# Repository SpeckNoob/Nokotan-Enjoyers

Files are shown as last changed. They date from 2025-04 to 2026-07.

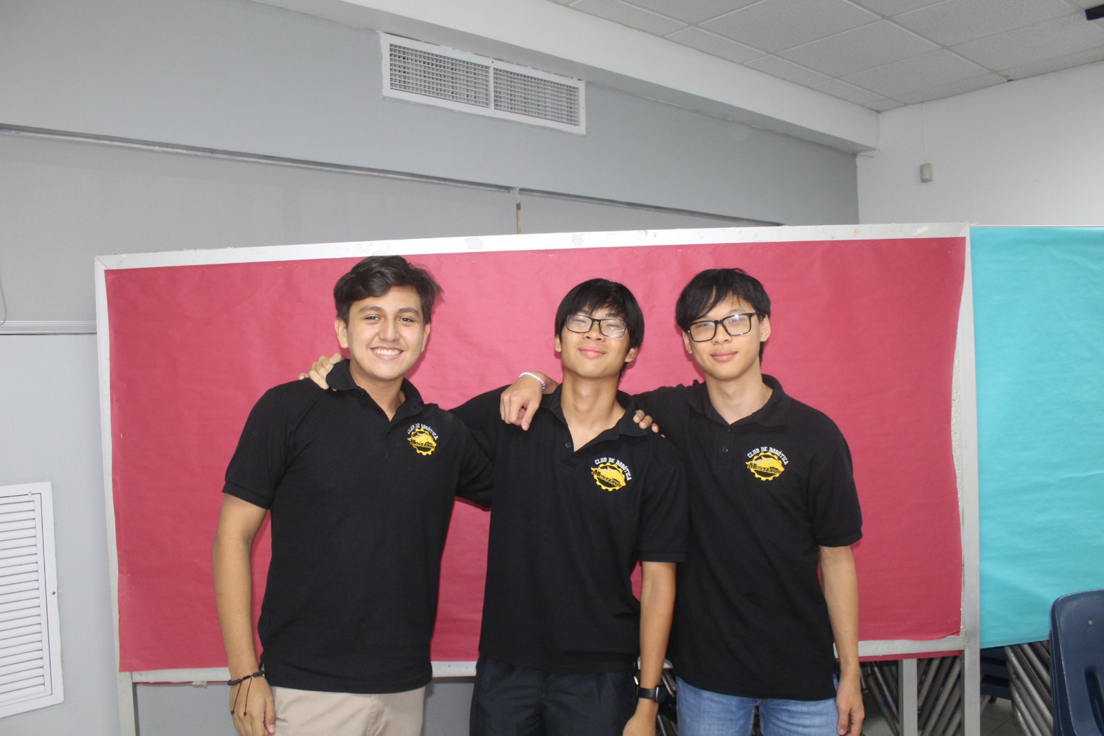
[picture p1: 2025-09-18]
t-photos/pictures/342e0a49-aa14-48cb-8f80-8e314d3dc333.jpeg

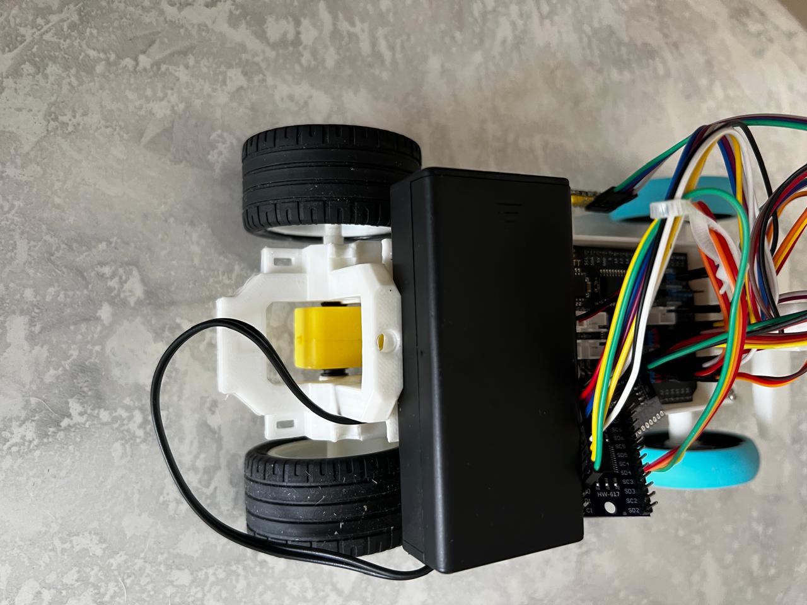
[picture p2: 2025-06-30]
v-photos/wro robot back.jpg

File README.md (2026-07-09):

Mustangs Down
====

<p align="center">
  Demo animation
</p>

This repository contains the documentation for the Mustangs Down team's robot for the 2025 World Robot Olympiad Future Engineers category competition. The robot was designed and built by a team of three.

Table of contents
----

- [The Team](#the-team)
- [The Competition](#the-competition)
- [Photos of the robot](#photos-of-the-robot)
  - [Video](#video)
- [Motors, sensors and systems](#motors-sensors-and-systems)
  - [Movement](#movement)
- [Steering](#steering)
  - [Servo Motor](#servo-motor)
- [Motherboard](#motherboard)
- [Skeleton/Chassis](#skeleton/chassis)
- [Energy Management](#energy-management)
  - [Battery](#battery)
- [Sensors](#sensors)
  - [Multiplexer](#multiplexer)
- [Circuit Diagram](#circuit-diagram)
- [Program and Source Code](#program-and-source-code)
  - [Drive](#drive)
  - [Open Round](#open-round)
  - [Obstacle Round](#obstacle-round)
  - [Camera](#camera)

## The Team
----

Mark Chen, Age: 16



School: Panamerican School of Panama, PAS

Hi!, I'm Mark from Panama with Chinese origin born in February 8 2009. I've been participating in WRO since 2022 and this is my second year participating in the Future Engineers category. I enjoy playing piano and I am a part of a school band, other hobbies include cubing (Rubik's cube competitions), gaming, drawing and volleyball.

----

Juan Pablo Gomez, Age: 16



School: Panamerican School of Panama, PAS

Hi, I'm Juan Pablo, from Colombia. I love robotics. I've been working with robots since I was 8 years old. My main hobbies are playing bass, hanging out with friends, playing video games, driving karts, and participating in various sports such as football and volleyball.

----

Julio Chong, Age: 16



School: Panamerican School of Panama, PAS

My name is Julio Chong, a panamenian teen with chinese antescedents who was born in August 24, 2008. I've been into robotics since 9th grade on 2023. My hobbies are playing the guitar, cooking, coding, learning new languages and also doing lots of exercise or sport, especially contact sports such as jiujitsu.

----

Victor Sanchez (Coach), Age: 35



School: Panamerican School of Panama, PAS

Hello, I'm Victor Sanchez, robotics profesor with experience in educational programming with LEGO SPIKE in Panamerican School, I've led the robotics scholar proyect for 4 years with the goal of becoming national champion in Panama and solid at an international scale. I enjoy woodworking and playing videogames.

----

Team photo
----



[Back to table of contents](#table-of-contents)

The competition
----

Unlike the structured missions of other WRO categories, Future Engineers presents a broad problem (often related to autonomous vehicles, smart systems, or complex automation), and teams must engineer a full solution. Teams work within defined technical limits (size, cost, sensors, etc.) that mimic real-life engineering conditions. This challenge has two main tasks, the first round which tests the robot's progamming of being able to drive many laps without crashing. The second round adds obstacles that the robot must avoid crashing into and a parking space where the robot should finish.

This challenge emphasizes all aspects of the engineering process, including:

- Mobility: Developing efficient vehicle movement.

- Obstacle managing: Detecting and dodging the different obstacles (Green and Red blocks) with effiency.

- Documentation: Showcasing engineering progress, design planning, and collaboration though a GitHub repository.

Points are awarded based on the performance of the robot. In the first round, points are awarded if the robot does not crash or stop during the round. In the second round, points are awarded for every obstacle the robot is able to detect and avoid, bonus points are rewarded if the robot can succesfully finish in the designated parking space.

[Back to table of contents](#table-of-contents)

## Photos of the robot
----

| Top | Bottom |
|---|---|
| WhatsApp Image 2025-09-29 at 17 31 00_9bd73e38 |WhatsApp Image 2025-09-29 at 17 31 00_5592dadc |

| Left | Right |
|---|---|
| WhatsApp Image 2025-09-29 at 17 31 00_614abe10 |WhatsApp Image 2025-09-29 at 17 31 00_24b984a5 |

| Front | Back |
|---|---|
|WhatsApp Image 2025-09-29 at 17 31 01_d4408ce1 |WhatsApp Image 2025-09-29 at 17 31 01_3e9ea6a2 |

## Video
---

Video of the robot on Youtube: [Video](https://youtu.be/vqMiVIuP070)

[Back to table of contents](#table-of-contents)

## Motors, sensors and systems
----

The robot operates with multiple motors and sensors which will be showcased here.

## Movement
----
The robot uses motors for drving and steering, these components work together to ensure the robot has a smooth and efficient movement.



|  Voltage | Current  | rpm |  Torque  |
|---|---|---|---|
| 3 | 160 | 120 | 0.45 |
| 6 | 220 | 200 | 1.0 |
| 7.2 | 250 | 250 | 1.5 |

We chose this motor because it was viable and the one we had already, other motors we used didn't hold up or didn't have enough power to move the wheels. Although there are way better motors we could've bought, we chose this one for its dual motor and it didn't need a driving axle. This made the building process a bit easier and less complicated.

The motor works by converting electrical energy into mechanical energy, specifically rotational motion, through the interaction of magnetic fields. It uses the principle that a current-carrying conductor experiences a force within a magnetic field. This force causes a rotor to spin, which then drives a shaft, producing mechanical work. This is then connected to the wheels with two jammed axles.

To connect the motor to the skeleton, we made an opening in the skeleton to fit the motor inside, then we held it up with a bent metal sheet and some screws.



The design could be perfected if the skeleton was made to scale with the motor or we had chosen a different motor that not only satisfies what the robot needs but also that it fits confortably to the skeleton.



(Full model is in the "models" repository)

## Steering
----
We experimented with many steering mechanisms but the one we found most success was anti-Ackerman steering. Other methods where either too big and complex or didn't turn the right amount. Anti-Ackerman systems are usually used on racing cars where the vehicles must turn at high speeds and the tires might slip, the outer tire’s increased steering angle helps compensate for these slip angles, maximizing grip during high-speed cornering. Even though with this robot we can't reach those speeds where the wheels start slipping, the anti-Ackerman system is still the most effective and simple for this competition.

The steering system is composed of two identicar wheel holders connected with two steering axels, these two axels are then connected to the servo motor in the middle.



## Servo motor:
----

 

|  Voltage | Temperature | Angle of Rotation | Torque |  Control signal  |  Type of Servo  |
|---|---|---|---|---|---|
|  3.3V~5V | -30°C~+60°C | 180 | 1.6KG/cm | PWM signal |  Digital servo  |

For the motor we used the Steren servo motor, it's an okay motor but we chose it because it was the one we had in hand. Although it is a cheap motor, it works perfectly with the design of the robot. It also operates on low voltage (4.8–6V) and provides moderate torque for small mechanisms.



The motor is placed between both axels to form an anti-ackerman system

## Motherboard
----



| Chip | Clock | ROM |  SRAM  |  FLASH  | Interfaces |  Input voltages  |
|---|---|---|---|---|---|---|
| ESP-WROOM-32 | 240MHz  |  448KB  |  520KB | 4MB |  UART , I2C , SPI , CAN  | 6-18V |

For motor driver, we chose the Acebott ESP32, it's capable of controling not only the motors but the sensors as well. It acts like a bridge between a microcontroller and motors, allowing us to safely control higher voltages and currents than the microcontroller can handle directly

## Skeleton/Chassis
----

This year, instead of making the chassis out of lego, we changed it to 3D printed since it allowed it to be less bulky and lighter unlike the lego version. It also allowed for more complex designs such as in the steering and motor placements, these modifications although harder to add to the robot, it immensely helped the functionality and efficiency of the robot. The model was first made in Tinkercad and later passed to Blender for final touches and took around 2 hours.



We had an accident not long before the competition and the piece that holds the camera broke, so we had to design a new piece that not only was more ressistant but also that gave the camera a better view, the piece was placed at the back of the robot and more elevated than the previous design.



## Energy management
----
## Battery:
----

We chose these batteries because they were small and easy to fit on the robot and they had good runtime compared to the lego spike brain. They also deliver higher electric outputs that could power the new motors we chose.



Model 18605

3.7 V

## Sensors
----

For the robot we used the OpenMV Cam RT62 which allowed the robot to detect walls and the colored blocks more easily. It's a small, low power, microcontroller board which allows you to easily implement applications using machine vision in the real-world. It is a huge improvement from last year's robot since we didn't have access to these type of sensors/camera. A camera gives a robot far more versatility than standard sensors, since it can capture detailed visual information to recognize objects, colors, and surroundings, while single-purpose sensors like ultrasonic or touch only provide narrow data such as distance, contact, or light levels.



Dimentions:

-Length: 45 mm

-Width: 36 mm

-Height: 29 mm

|  Microcontroler | Flash memory |  RAM | Frequency |  Resolution  |  FPS  | Weight |
|---|---|---|---|---|---|---|
|  ISSI2232  | 32MB | 512KB | 600 MHz | 2592 x 1944 |  40  | 20g |

## Multiplexer
----



For a multiplexer we chose the TCA9548A I2C multiplexer, which allows you to communicate with up to 8 I2C devices with the same I2C bus.

Main features:

-1 to 8 bidireccional translating switches

-Active-low reset input

-Three address pins—up to 8 TCA9548A devices on the same I2C bus

-Channel selection through an I2C bus

-Operating power supply voltage range: 1.65V to 5.5V

-5V tolerant pins

[Back to table of contents](#table-of-contents)

## Circuit diagram
----

electric diagram WRO (1)

Pins used:

electric diagram WRO (2)

[Back to table of contents](#table-of-contents)

## Program and source code
----

For programing the robot, we used both Python and Arduino coding languages. Python because the program for the camera required Python usage and it allowed us to have more precise movements, Pyhton is easy to learn, highly versatile, and widely supported: its simple, readable syntax lowers the entry barrier for beginners, yet it’s powerful enough for professionals to use in fields like AI, data science, web development, robotics, and automation. We used Arduino because we wanted to use a ESP32 motor driver which was more viable and more precise than other models. Arduino is good for programming because it’s simple, beginner-friendly, and lets you quickly control hardware like sensors and motors to build real-world projects.

Code for each component
----

Drive
----

For driving, the code works by constantly making the car move forward and stopping once all three laps of the track are completed.

```python

void MoveForward() {
  digitalWrite(EN_PIN, LOW);
  digitalWrite(STCP_PIN, LOW);
  shiftOut(DATA_PIN, SHCP_PIN, MSBFIRST, M1_Forward);
  digitalWrite(STCP_PIN, HIGH);
  digitalWrite(PWM1_PIN, HIGH);  // Encender PWM a tope
}

void StopMotor() {
  digitalWrite(PWM1_PIN, LOW);  // Apagar PWM
}
```
Additionaly, a part of the code specifies the maximum amount of time that the code can run.

```python

// Control de tiempo
#define TIEMPO_LIMITE_MS 67000  // 1 minuto, 7 segundos
unsigned long tiempoInicio;
bool detenido = false;
```

Servo motor
----

The servo motor is supported by the distance sensors in both right and left sides of the robot, the servo moves accordingly wether the sensors detect a wall on the left or right, additionaly, at the end it stops for a certain amount of time so the robot does not perform more than 3 laps.

```python

  // Servo
  miServo.setPeriodHertz(50);
  miServo.attach(SERVO_PIN, 500, 2400);
  miServo.write(SERVO_CENTER);

  // Sensor izquierdo
  selectOnlyOneMux(MUX_LEFT_ADDR);
  sensorLeft.setTimeout(500);
  if (!sensorLeft.init()) {
    Serial.println("Error: sensor izquierdo no detectado.");
    while (1);
  }
  sensorLeft.setDistanceMode(VL53L1X::Long);
  sensorLeft.setMeasurementTimingBudget(20000);
  sensorLeft.startContinuous(20);

  // Sensor derecho
  selectOnlyOneMux(MUX_RIGHT_ADDR);
  sensorRight.setTimeout(500);
  if (!sensorRight.init()) {
    Serial.println("Error: sensor derecho no detectado.");
    while (1);
  }
  sensorRight.setDistanceMode(VL53L1X::Long);
  sensorRight.setMeasurementTimingBudget(50000);
  sensorRight.startContinuous(50);

  Serial.println("Sistema listo.");

  // Tiempo inicial
  tiempoInicio = millis();
}

void loop() {
  // Verificar si se superó el tiempo límite
  if (!detenido && millis() - tiempoInicio >= TIEMPO_LIMITE_MS) {
    Serial.println("Tiempo límite alcanzado. Deteniendo todo.");
    StopMotor();
    miServo.write(SERVO_CENTER);

```

The sensors detect the distance from the wall to the robot and responds accordingly, the servo motor will activate if the robot is 80cm or closer to the wall.

```python

  // Leer sensor izquierdo
  selectOnlyOneMux(MUX_LEFT_ADDR);
  int distLeft = sensorLeft.read();
  if (sensorLeft.timeoutOccurred()) {
    Serial.println("Timeout sensor izquierdo");
    distLeft = 0;
  }

  // Leer sensor derecho
  selectOnlyOneMux(MUX_RIGHT_ADDR);
  int distRight = sensorRight.read();
  if (sensorRight.timeoutOccurred()) {
    Serial.println("Timeout sensor derecho");
    distRight = 0;
  }

  Serial.print("Izquierdo: "); Serial.print(distLeft);
  Serial.print(" mm | Derecho: "); Serial.println(distRight);

  // Reacción del servo con prioridad
  if (distLeft > OBSTACLE_THRESHOLD) {
    Serial.println("Distancia izquierda > 80 cm → girar a la izquierda");

  StopMotor();  // Prioriza el servo
    delay(100);
    miServo.write(SERVO_LEFT);
    delay(2800);
    miServo.write(SERVO_CENTER);
    delay(200);
    MoveForward();  // Reanuda motor
  } 
  else if (distRight > OBSTACLE_THRESHOLD) {
    Serial.println("Distancia derecha > 80 cm → girar a la derecha");

```

## Open Round
----

At the start of the round and after every turn, the robot ignores any readings that are one meter or further for two seconds. The sensor has to read a distance of more than 1.2 meters to make a turn, if the sensor on the left detects a distance of more than 1.2 meters, the robot will turn left. After three laps the robot will stop in the same spot that it started, at the start of the round the robot is given a number value of 0 and it increases by 1 every time it makes a lap, after 12 laps (sections) the robot will stop at the position that the value of 0 was given. By using this method, the robot is more stable when it comes to making the turns and also avoids getting too close to the walls.

```python

Ronda abierta
#include <Wire.h>
#include <VL53L1X.h>
#include <ESP32Servo.h>
#include "Arduino.h"

// Multiplexores
#define MUX_LEFT_ADDR  0x70
#define MUX_RIGHT_ADDR 0x74
#define MUX_CHANNEL_0  0

// Sensores
VL53L1X sensorLeft;
VL53L1X sensorRight;

// Servo Steam
#define SERVO_PIN 25
#define SERVO_LEFT     15
#define SERVO_CENTER   37
#define SERVO_RIGHT    55
Servo miServo;

// Motor control con shift register
#define SHCP_PIN 18
#define EN_PIN   16
#define DATA_PIN 5
#define STCP_PIN 17
#define PWM1_PIN 19
int M1_Forward = 128;

// Umbral: 1000 mm
#define OBSTACLE_THRESHOLD 1000

int contadorGiros = 0;
bool detenido = false;
unsigned long tiempoInicioRecta = 0;

void selectOnlyOneMux(uint8_t muxAddr) {
  Wire.beginTransmission(MUX_LEFT_ADDR); Wire.write(0x00); Wire.endTransmission();
  Wire.beginTransmission(MUX_RIGHT_ADDR); Wire.write(0x00); Wire.endTransmission();
  Wire.beginTransmission(muxAddr); Wire.write(1 << MUX_CHANNEL_0); Wire.endTransmission();
  delay(2);
}

void MoveForward() {
  digitalWrite(EN_PIN, LOW);
  digitalWrite(STCP_PIN, LOW);
  shiftOut(DATA_PIN, SHCP_PIN, MSBFIRST, M1_Forward);
  digitalWrite(STCP_PIN, HIGH);
  digitalWrite(PWM1_PIN, HIGH);
}

void StopMotor() {
  digitalWrite(PWM1_PIN, LOW);
}

int lecturaFiltrada(VL53L1X &sensor, uint8_t muxAddr, unsigned long referencia) {
  selectOnlyOneMux(muxAddr);
  int lectura = sensor.read();
  if (lectura <= 0) return 0;
  if ((millis() - referencia < 1800) && lectura > OBSTACLE_THRESHOLD) return 0;
  return lectura;
}

void setup() {
  Serial.begin(115200);
  Wire.begin();

  // Pines motor
  pinMode(SHCP_PIN, OUTPUT);
  pinMode(EN_PIN, OUTPUT);
  pinMode(DATA_PIN, OUTPUT);
  pinMode(STCP_PIN, OUTPUT);
  pinMode(PWM1_PIN, OUTPUT);

  // Servo
  miServo.setPeriodHertz(50);
  miServo.attach(SERVO_PIN, 500, 2400);
  miServo.write(SERVO_CENTER);

  // Sensor izquierdo
  selectOnlyOneMux(MUX_LEFT_ADDR);
  sensorLeft.setTimeout(250);
  sensorLeft.init();
  sensorLeft.setDistanceMode(VL53L1X::Long);
  sensorLeft.setMeasurementTimingBudget(33000);
  sensorLeft.startContinuous(33);

  // Sensor derecho
  selectOnlyOneMux(MUX_RIGHT_ADDR);
  sensorRight.setTimeout(250);
  sensorRight.init();
  sensorRight.setDistanceMode(VL53L1X::Long);
  sensorRight.setMeasurementTimingBudget(33000);
  sensorRight.startContinuous(33);

  tiempoInicioRecta = millis();
  Serial.println("Sistema listo.");
}

void loop() {
  if (detenido) return;

  int distLeft = lecturaFiltrada(sensorLeft, MUX_LEFT_ADDR, tiempoInicioRecta);
  int distRight = lecturaFiltrada(sensorRight, MUX_RIGHT_ADDR, tiempoInicioRecta);

  Serial.print("Izquierdo: "); Serial.print(distLeft); Serial.print(" mm | ");
  Serial.print("Derecho: "); Serial.println(distRight);

  bool giroRealizado = false;

  if (distLeft > OBSTACLE_THRESHOLD) {
    Serial.println("→ Gira a la izquierda");
    StopMotor();
    delay(100);
    miServo.write(SERVO_LEFT);
    delay(2800);
    miServo.write(SERVO_CENTER);
    delay(150);
    MoveForward();
    contadorGiros++;
    tiempoInicioRecta = millis();  // Reinicia tiempo de filtro
    giroRealizado = true;
  }

  if (distRight > OBSTACLE_THRESHOLD) {
    Serial.println("→ Gira a la derecha");
    StopMotor();
    delay(100);
    miServo.write(SERVO_RIGHT);
    delay(2800);
    miServo.write(SERVO_CENTER);
    delay(150);
    MoveForward();
    contadorGiros++;
    tiempoInicioRecta = millis();  // Reinicia tiempo de filtro
    giroRealizado = true;
  }

  if (!giroRealizado) {
    MoveForward();
  }

  if (contadorGiros >= 12) {
    Serial.println("✔ 12 giros completados. Avanzando y deteniendo...");
    MoveForward();
    delay(1000);
    StopMotor();
    miServo.write(SERVO_CENTER);
    digitalWrite(STCP_PIN, LOW);
    shiftOut(DATA_PIN, SHCP_PIN, MSBFIRST, 0x00);
    digitalWrite(STCP_PIN, HIGH);
    digitalWrite(PWM1_PIN, LOW);
    detenido = true;
  }

  delay(60);  // Lecturas rápidas
}

```

Open round (FINAL)
----

This is the last update to the code before the 2025 national competition in Panama, it is the most refined and updated version of the previous code.

```python

#include <Wire.h>
#include <VL53L1X.h>
#include <ESP32Servo.h>
#include "Arduino.h"

// =================== Parámetros clave ===================
#define ABS_OPEN_MM                 2300   // umbral “lado abierto” hacia ~3 m (ajusta 2100–2700)
#define DELTA_OPEN_MM                600   // apertura relativa vs. línea base del lado fijo (500–800)
#define TURN_MS                     2875   // giro con motor encendido (tu valor)
#define LOOP_DELAY_MS                 10   // bucle rápido
#define ARM_DELAY_MS                 100   // pequeña desensibilización tras cada giro
#define START_IGNORE_MS              800   // ignorar lecturas grandes al iniciar (0.8 s)
#define POST_FIRST_TURN_IGNORE_MS   1600   // ignorar lecturas grandes tras CADA giro (ajustable)
// ========================================================

// Multiplexores
#define MUX_LEFT_ADDR  0x70
#define MUX_RIGHT_ADDR 0x74
#define MUX_CHANNEL_0  0

// Sensores
VL53L1X sensorLeft;
VL53L1X sensorRight;

// Servo
#define SERVO_PIN     25
#define SERVO_LEFT    10
#define SERVO_CENTER  35
#define SERVO_RIGHT   60
Servo miServo;

// Motor con shift register
#define SHCP_PIN 18
#define EN_PIN   16
#define DATA_PIN 5
#define STCP_PIN 17
#define PWM1_PIN 19
int M1_Forward = 128;

// Estado y filtros
int  contadorGiros     = 0;
bool detenido          = false;
enum Dir { NONE=0, LEFT=1, RIGHT=2 };
Dir fixedDir           = NONE;

float emaL=0, emaR=0; bool emaL_ok=false, emaR_ok=false;
unsigned long lastTurnTS    = 0;         // para ARM_DELAY_MS
unsigned long ignoreUntilTS = 0;         // ventana para ignorar lecturas grandes

// ---------- Utilidades ----------
static inline void selectOnlyOneMux(uint8_t muxAddr) {
  Wire.beginTransmission(MUX_LEFT_ADDR);  Wire.write(0x00); Wire.endTransmission();
  Wire.beginTransmission(MUX_RIGHT_ADDR); Wire.write(0x00); Wire.endTransmission();
  Wire.beginTransmission(muxAddr);        Wire.write(1 << MUX_CHANNEL_0); Wire.endTransmission();
  delayMicroseconds(500);
}

static inline void MoveForward() {
  digitalWrite(EN_PIN, LOW);
  digitalWrite(STCP_PIN, LOW);
  shiftOut(DATA_PIN, SHCP_PIN, MSBFIRST, M1_Forward);
  digitalWrite(STCP_PIN, HIGH);
  digitalWrite(PWM1_PIN, HIGH);  // motor encendido
}

static inline void StopMotor() {
  digitalWrite(PWM1_PIN, LOW);
}

static inline int readVL(VL53L1X &sensor, uint8_t muxAddr) {
  selectOnlyOneMux(muxAddr);
  int d = sensor.read();
  return d > 0 ? d : 0;  // ignora inválidos
}

static inline void updEMA(float &ema, bool &ok, int x) {
  if (x <= 0) return;
  const float a = 0.20f;                 // EMA_ALPHA
  if (!ok) { ema = x; ok = true; }
  else      { ema = a*x + (1.0f - a)*ema; }
}

// ---------- Giros con motor encendido ----------
void girarIzquierda() {
  Serial.println("→ Giro IZQUIERDA (motor encendido)");
  miServo.write(SERVO_LEFT);
  MoveForward();
  delay(TURN_MS);
  miServo.write(SERVO_CENTER);
  delay(80);
  MoveForward();
  contadorGiros++;
  lastTurnTS = millis();
  // Tras CADA giro: activar ventana de ignorar lecturas grandes
  ignoreUntilTS = millis() + POST_FIRST_TURN_IGNORE_MS;
}

void girarDerecha() {
  Serial.println("→ Giro DERECHA (motor encendido)");
  miServo.write(SERVO_RIGHT);
  MoveForward();
  delay(TURN_MS);
  miServo.write(SERVO_CENTER);
  delay(80);
  MoveForward();
  contadorGiros++;
  lastTurnTS = millis();
  // Tras CADA giro: activar ventana de ignorar lecturas grandes
  ignoreUntilTS = millis() + POST_FIRST_TURN_IGNORE_MS;
}

// ---------- Setup ----------
void setup() {
  Serial.begin(115200);
  Wire.begin();

  // Pines motor
  pinMode(SHCP_PIN, OUTPUT);
  pinMode(EN_PIN,  OUTPUT);
  pinMode(DATA_PIN, OUTPUT);
  pinMode(STCP_PIN, OUTPUT);
  pinMode(PWM1_PIN, OUTPUT);

  // Servo
  miServo.setPeriodHertz(50);
  miServo.attach(SERVO_PIN, 500, 2400);
  miServo.write(SERVO_CENTER);

  // ===== Sensores ToF: Long + 25 ms =====
  selectOnlyOneMux(MUX_LEFT_ADDR);
  sensorLeft.setTimeout(250);
  sensorLeft.init();
  sensorLeft.setDistanceMode(VL53L1X::Long);
  sensorLeft.setMeasurementTimingBudget(25000);
  sensorLeft.startContinuous(25);

  selectOnlyOneMux(MUX_RIGHT_ADDR);
  sensorRight.setTimeout(250);
  sensorRight.init();
  sensorRight.setDistanceMode(VL53L1X::Long);
  sensorRight.setMeasurementTimingBudget(25000);
  sensorRight.startContinuous(25);

  // Ventana inicial: ignorar lecturas grandes por 0.8 s
  ignoreUntilTS = millis() + START_IGNORE_MS;

  Serial.println("Listo: dir fija, giro con motor, y ventanas de ignorar tras CADA giro.");
}

// ---------- Loop ----------
void loop() {
  if (detenido) return;

  const unsigned long now = millis();
  const bool ignoringLarge = (now < ignoreUntilTS);               // ventana activa
  const bool armedTime     = (now - lastTurnTS) >= ARM_DELAY_MS;  // pequeño re-armado
  const bool canTurn       = (!ignoringLarge) && armedTime;       // condición global

  int dL = readVL(sensorLeft,  MUX_LEFT_ADDR);
  int dR = readVL(sensorRight, MUX_RIGHT_ADDR);

  // Actualiza líneas base
  updEMA(emaL, emaL_ok, dL);
  updEMA(emaR, emaR_ok, dR);

  // Log útil
  Serial.print("L: "); Serial.print(dL); Serial.print(" (EMA ");
  Serial.print(emaL_ok ? (int)emaL : -1); Serial.print(") | R: ");
  Serial.print(dR); Serial.print(" (EMA ");
  Serial.print(emaR_ok ? (int)emaR : -1); Serial.print(") | IGNORING=");
  Serial.println(ignoringLarge ? "YES" : "NO");

  // Detección (abs/rel) condicionada por canTurn
  bool leftAbs  = canTurn && (dL >= ABS_OPEN_MM);
  bool rightAbs = canTurn && (dR >= ABS_OPEN_MM);
  bool leftRel  = canTurn && (emaL_ok && (dL - emaL) >= DELTA_OPEN_MM);
  bool rightRel = canTurn && (emaR_ok && (dR - emaR) >= DELTA_OPEN_MM);

  // 1) Si aún no hay dirección fija: decide en el primer evento válido
  if (fixedDir == NONE && canTurn) {
    bool L = leftAbs  || leftRel;
    bool R = rightAbs || rightRel;
    if (L || R) {
      if (L && R) fixedDir = (dL >= dR) ? LEFT : RIGHT;
      else        fixedDir =  L ? LEFT : RIGHT;
      Serial.print("Dirección FIJA: "); Serial.println(fixedDir == LEFT ? "IZQUIERDA" : "DERECHA");
      if (fixedDir == LEFT)  girarIzquierda();
      else                   girarDerecha();
      return;
    }
  }
  // 2) Con dirección fija: SOLO miramos ese lado y respetamos la ventana/armado
  else if (canTurn) {
    if (fixedDir == LEFT) {
      if (leftAbs || leftRel) { girarIzquierda(); return; }
    } else { // RIGHT
      if (rightAbs || rightRel) { girarDerecha(); return; }
    }
  }

  // Avanza recto si no se dispara el giro
  MoveForward();

  if (contadorGiros >= 12) {
    Serial.println("✔ 12 giros completados. Avanzando y deteniendo...");
    MoveForward();
    delay(1000);
    StopMotor();
    miServo.write(SERVO_CENTER);
    digitalWrite(STCP_PIN, LOW);
    shiftOut(DATA_PIN, SHCP_PIN, MSBFIRST, 0x00);
    digitalWrite(STCP_PIN, HIGH);
    digitalWrite(PWM1_PIN, LOW);
    detenido = true;
  }

  delay(LOOP_DELAY_MS);
}

```

Obstacle round
----

For the obstacle round, the camera was the main component. It is capable of detecting colors and objects from a distance and act accordingly, the distance sensors also play the same role and are still in use for this round. 

The camera detects the green and red blocks and the robot then knows where to turn and when, then it checks the distance sensors to see if it has space or the need to turn, the rest of the code is mostly the same with some slight modifications so the camera could work. 

Video of the robot on Youtube: [Video](https://youtube.com/shorts/kXKS2O0ia2E?feature=share)

```python

void loop() {
  // UART desde cámara: color detectado
  if (Serial1.available() && !enGiroPorColor) {
    String color = Serial1.readStringUntil('\n');
    color.trim();

    if (color == "ROJO") {
      Serial.println("Color ROJO detectado → giro a la derecha");
      ejecutarGiroColor(SERVO_RIGHT, SERVO_LEFT);
    }
    else if (color == "VERDE") {
      Serial.println("Color VERDE detectado → giro a la izquierda");
      ejecutarGiroColor(SERVO_LEFT, SERVO_RIGHT);
    }
  }

  MoveForward();  // Siempre avanza a media velocidad

  // Lectura sensores de distancia
  selectOnlyOneMux(MUX_LEFT_ADDR);
  int distLeft = sensorLeft.read();
  if (sensorLeft.timeoutOccurred()) {
    Serial.println("Timeout sensor izquierdo");
    distLeft = 0;
  }

  selectOnlyOneMux(MUX_RIGHT_ADDR);
  int distRight = sensorRight.read();
  if (sensorRight.timeoutOccurred()) {
    Serial.println("Timeout sensor derecho");
    distRight = 0;
  }

```

(Update) The information that the camera recieves is passed to UART, then the camera only looks for green and red blocks and only detects the color that is closest, that information is then passed to UART

```python

from machine import UART
import sensor, image, time

uart = UART(1, baudrate=115200)

sensor.reset()
sensor.set_pixformat(sensor.RGB565)
sensor.set_framesize(sensor.QQVGA)  # Baja calidad para más FPS
sensor.skip_frames(time=2000)
sensor.set_auto_gain(False)
sensor.set_auto_whitebal(False)

red_threshold = (30, 100, 15, 127, 15, 127)
green_threshold = (30, 100, -127, -15, 15, 127)

ultimo_color = ""
tiempo_ultimo_envio = time.ticks_ms()
intervalo = 10000  # 10 segundos

while True:
    img = sensor.snapshot()

    rojos = img.find_blobs([red_threshold], pixels_threshold=100, area_threshold=100, merge=True)
    verdes = img.find_blobs([green_threshold], pixels_threshold=100, area_threshold=100, merge=True)

    blob_rojo = max(rojos, key=lambda b: b.pixels(), default=None)
    blob_verde = max(verdes, key=lambda b: b.pixels(), default=None)

    color_detectado = ""
    if blob_rojo and not blob_verde:
        color_detectado = "ROJO"
    elif blob_verde and not blob_rojo:
        color_detectado = "VERDE"
    elif blob_rojo and blob_verde:
        if blob_rojo.pixels() > blob_verde.pixels():
            color_detectado = "ROJO"
        else:
            color_detectado = "VERDE"

    if color_detectado:
        tiempo_actual = time.ticks_ms()
        if (color_detectado != ultimo_color) or (time.ticks_diff(tiempo_actual, tiempo_ultimo_envio) > intervalo):
            uart.write(color_detectado + "\n")
            print("Color enviado:", color_detectado)
            ultimo_color = color_detectado
            tiempo_ultimo_envio = tiempo_actual
    else:
        ultimo_color = ""  # Reiniciar si no hay detección

```

This last part is to ensure the robot does not crash into any wall or block after turning or overturning. It also checks with the distance sensors one more time so it does not misalign from the track's path.

```python

  Serial.print("Izquierdo: "); Serial.print(distLeft);
  Serial.print(" mm | Derecho: "); Serial.println(distRight);

  if (!enGiroPorColor) {
    if (distLeft > OBSTACLE_THRESHOLD) {
      Serial.println("Distancia izquierda > 100 cm → giro a la izquierda");
      StopMotor();
      delay(100);
      miServo.write(SERVO_LEFT);
      delay(2800);
      miServo.write(SERVO_CENTER);
      delay(200);
      MoveForward();
    } else if (distRight > OBSTACLE_THRESHOLD) {
      Serial.println("Distancia derecha > 100 cm → giro a la derecha");
      StopMotor();
      delay(100);
      miServo.write(SERVO_RIGHT);
      delay(2800);
      miServo.write(SERVO_CENTER);
      delay(200);
      MoveForward();
    }
  }

  delay(100);
}
```

Obstacle round (FINAL)

This is the last update to the code before the 2025 national competition in Panama, many components of the previous code were changed for the robot to detect and see the colored blocks more accurately (Each section is highlighted).

```python

/****************************************************
 *  ROBOT 3x3 – ESP32 (Motores + Servo + VL53L1X + Cam UART)
 *  - Secuencia de salida y maniobra final
 *  - Lógica de colores HORARIO y ANTIHORARIO (completa)
 *  - Maniobra especial + reintento del mismo índice
 *  - Memoria de vuelta 1 (colores usados) → reproducir vuelta 2 y 3
 ****************************************************/

#include <Wire.h>
#include <VL53L1X.h>
#include <ESP32Servo.h>
#include "Arduino.h"

// =================== Multiplexores / VL53 ===================
#define MUX_LEFT_ADDR   0x70
#define MUX_RIGHT_ADDR  0x74
#define MUX_CHANNEL_0   0
VL53L1X sensorLeft, sensorRight;

// =================== Servo ===================
#define SERVO_PIN        25
#define SERVO_LEFT        5
#define SERVO_CENTER     35   // centro "normal" (luego de terminar en giro a la DER)
#define SERVO_CENTER_L   45   // centro "luego de terminar en giro a la IZQ"
#define SERVO_RIGHT      75
Servo miServo;

// =================== Motor (shift register) ===================
#define SHCP_PIN 18
#define EN_PIN   16
#define DATA_PIN 5
#define STCP_PIN 17
#define PWM1_PIN 19
const int M1_Forward = 128;
const int M1_Reverse = 64;
const int M1_Stop    = 0;

// =================== UART CÁMARA (Serial1: RX=3, TX=1) ===================
#define CAM_BAUD 115200
#define CAM_RX   3
#define CAM_TX   1

// =================== Parámetros (MODULAR) ===================
// Micro-pasos salida
#define PASO_AVANZAR_MS      250
#define PASO_RETRO_MS        230
#define PAUSA_MS             150
#define ESTABILIZA_MS        130

// Maniobra final (giro contrario)
#define FINAL_PRE_AVANCE_MS  300
#define FINAL_AVANZAR_MS     1600
#define FINAL_RETRO1_MS       500
#define FINAL_AVANZAR2_MS     600
#define FINAL_RETRO2_MS      1000

// Timings base de colores
#define GREEN1_LEFT_MS       1400  // 1.4 s (Ajustado a tu última tabla de horario 1.º=VERDE)
#define GREEN1_RIGHT_MS      1400
#define GREEN1_RIGHT2_MS     2800
#define GREEN1_FINAL_RETRO   1000
#define GREEN1_MID_RETRO      500   // retro tras centro en 1.º=VERDE (horario)

#define RED1_RIGHT_MS        1600
#define RED1_LEFT_MS         1600

#define SEG_1S               1000
#define SEG_2S               2000
#define GIRO_LARGO_MS        2800   // 2.8 s (giro largo)

// Avances/generales
#define CONT_TURN_MS         2000   // 2.0 s para tramos simétricos
#define CONT_FORWARD_MS      2000
#define RETRO_CORTO_MS        300
#define RETRO_LARGO_MS       2000

// Timeouts SOLO en ramas que admiten "NINGUNO"
#define WAIT_NO_COLOR_MS    10000

// Salida del estacionamiento (ciclos)
#define NUM_CICLOS_IZQ  9   // izquierda (antiho) – micro-ciclos
#define NUM_CICLOS_DER  6   // derecha  (horario) – micro-ciclos

// =================== Estado global ===================
enum Sentido { HORARIO=0, ANTIHORARIO=1 };
Sentido sentido = HORARIO;  // se fija tras la salida

// Memoria de colores “usados” por la lógica (vuelta 1)
char memColores[9];           // índices 1..8 (‘G’, ‘R’, ‘N’)
bool memoriaLlena = false;

// Control de vueltas
uint8_t vueltaActual = 1;     // 1, 2, 3
bool usarMemoria = false;     // true en vueltas 2 y 3

// =================== Utilidades MUX ===================
void selectOnlyOneMux(uint8_t muxAddr) {
  Wire.beginTransmission(MUX_LEFT_ADDR);  Wire.write(0x00); Wire.endTransmission();
  Wire.beginTransmission(MUX_RIGHT_ADDR); Wire.write(0x00); Wire.endTransmission();
  Wire.beginTransmission(muxAddr);        Wire.write(1 << MUX_CHANNEL_0);  Wire.endTransmission();
  delay(2);
}

// =================== Motores ===================
void MoveMotor(int dir, int speed) {
  if (speed < 0)   speed = 0;
  if (speed > 255) speed = 255;
  digitalWrite(EN_PIN, LOW);
  analogWrite(PWM1_PIN, speed);
  digitalWrite(STCP_PIN, LOW);
  shiftOut(DATA_PIN, SHCP_PIN, MSBFIRST, dir);
  digitalWrite(STCP_PIN, HIGH);
}

void MoveForward() {
  digitalWrite(EN_PIN, LOW);
  digitalWrite(STCP_PIN, LOW);
  shiftOut(DATA_PIN, SHCP_PIN, MSBFIRST, M1_Forward);
  digitalWrite(STCP_PIN, HIGH);
  digitalWrite(PWM1_PIN, HIGH);
}

void StopMotor() {
  analogWrite(PWM1_PIN, 0);
  digitalWrite(STCP_PIN, LOW);
  shiftOut(DATA_PIN, SHCP_PIN, MSBFIRST, M1_Stop);
  digitalWrite(STCP_PIN, HIGH);
}

void retro(int ms) {
  MoveMotor(M1_Reverse, 128);
  delay(ms);
  StopMotor();
}

// =================== Movimientos compuestos ===================
void avanzarRecto(int ms, int centro) {
  StopMotor();
  miServo.write(centro);
  delay(ESTABILIZA_MS);
  MoveForward();
  delay(ms);
  StopMotor();
}
void avanzarConGiro(int angServo, int ms) {
  StopMotor();
  miServo.write(angServo);
  delay(ESTABILIZA_MS);
  MoveForward();
  delay(ms);
  StopMotor();
}
inline void giroLargoHorario()    { avanzarConGiro(SERVO_RIGHT, GIRO_LARGO_MS); }
inline void giroLargoAntiHorario(){ avanzarConGiro(SERVO_LEFT,  GIRO_LARGO_MS); }

void servoCentroTrasDer() { miServo.write(SERVO_CENTER);   delay(ESTABILIZA_MS); }
void servoCentroTrasIzq() { miServo.write(SERVO_CENTER_L); delay(ESTABILIZA_MS); }

// =================== Cámara ===================
void limpiarBufferCamara() { while (Serial1.available()) Serial1.read(); }

char leerColorBloqueante() {
  limpiarBufferCamara();
  for (;;) {
    if (Serial1.available()) {
      String t = Serial1.readStringUntil('\n');
      t.trim(); t.toLowerCase();
      if (t == "verde") return 'G';
      if (t == "rojo")  return 'R';
    }
    delay(2);
  }
}

char leerColorConTimeout(unsigned long timeout_ms) {
  limpiarBufferCamara();
  unsigned long t0 = millis();
  while (millis() - t0 < timeout_ms) {
    if (Serial1.available()) {
      String t = Serial1.readStringUntil('\n');
      t.trim(); t.toLowerCase();
      if (t == "verde") return 'G';
      if (t == "rojo")  return 'R';
    }
    delay(2);
  }
  return 'N';
}

// Interfaz de lectura para vivo/memoria
char leerColorPaso(uint8_t idx, bool permitirNinguno, unsigned long to_ms) {
  if (usarMemoria) {
    char c = memColores[idx];
    Serial.print("[MEM paso "); Serial.print(idx); Serial.print("] -> ");
    Serial.println(c);
    return c;
  } else {
    char c = permitirNinguno ? leerColorConTimeout(to_ms) : leerColorBloqueante();
    // Guardar en memoria vuelta 1
    if (vueltaActual == 1) memColores[idx] = c;
    return c;
  }
}

// =================== Medición distancia (para salida) ===================
int lecturaSimple(VL53L1X &sensor, uint8_t muxAddr) {
  selectOnlyOneMux(muxAddr);
  int v = sensor.read();
  return (v > 0) ? v : 0;
}
int lecturaPromedio(VL53L1X &sensor, uint8_t muxAddr, uint8_t n=3) {
  long s=0; uint8_t val=0;
  for (uint8_t i=0;i<n;i++) { int x=lecturaSimple(sensor,muxAddr); if (x>0){s+=x;val++;} delay(10); }
  if (!val) return 0;
  return (int)(s/val);
}

// =================== Secuencia de salida (micro-ciclos) ===================
inline void microCiclo(int angLado, int centroAlVolver) {
  avanzarConGiro(angLado, PASO_AVANZAR_MS);
  miServo.write(centroAlVolver);
  delay(ESTABILIZA_MS);
  retro(PASO_RETRO_MS);
  delay(PAUSA_MS);
}
void secuenciaSalidaIzquierda() { // antiho
  for (uint8_t i=0;i<NUM_CICLOS_IZQ;i++) microCiclo(SERVO_LEFT, SERVO_CENTER_L);
}
void secuenciaSalidaDerecha() { // horario
  for (uint8_t i=0;i<NUM_CICLOS_DER;i++) microCiclo(SERVO_RIGHT, SERVO_CENTER);
}

// =================== Maniobra final (giro contrario al lado elegido) ===================
void maniobraFinal(bool eligioIzquierda) {
  // 1) Recto 0.3 s
  avanzarRecto(FINAL_PRE_AVANCE_MS, SERVO_CENTER);

  // 2) Giro contrario 1.6 s
  const bool contrarioEsIzq = !eligioIzquierda;
  const int angContrario = contrarioEsIzq ? SERVO_LEFT : SERVO_RIGHT;
  const int centroSegun = contrarioEsIzq ? SERVO_CENTER_L : SERVO_CENTER;
  avanzarConGiro(angContrario, FINAL_AVANZAR_MS);

  // 3) Centro y retro 0.5 s
  miServo.write(centroSegun); delay(ESTABILIZA_MS);
  retro(FINAL_RETRO1_MS);

  // 4) Mismo giro 0.6 s
  avanzarConGiro(angContrario, FINAL_AVANZAR2_MS);

  // 5) Centro y retro 1.0 s
  miServo.write(centroSegun); delay(ESTABILIZA_MS);
  retro(FINAL_RETRO2_MS);
}

// =================== Maniobras Especiales ===================
// HORARIO: NINGUNO → IZQ 0.5 → DER 0.5 → DER 2.8 → centro → retro 2.0
void maniobraEspecialHorario() {
  // IZQ 0.5
  avanzarConGiro(SERVO_LEFT, 500);
  // DER 0.5
  avanzarConGiro(SERVO_RIGHT, 500);
  // DER 2.8
  giroLargoHorario();
  // centro+retro 2.0
  servoCentroTrasDer();
  retro(RETRO_LARGO_MS);
}
// ANTIHORARIO: NINGUNO → DER 0.5 → IZQ 0.5 → IZQ 2.8 → centro(45) → retro 2.0
void maniobraEspecialAntiHo() {
  // DER 0.5
  avanzarConGiro(SERVO_RIGHT, 500);
  // IZQ 0.5
  avanzarConGiro(SERVO_LEFT, 500);
  // IZQ 2.8
  giroLargoAntiHorario();
  // centro+retro 2.0
  servoCentroTrasIzq();
  retro(RETRO_LARGO_MS);
}

// =================== Núcleo de lógica: HORARIO ===================
void ejecutarHorario() {
  Serial.println("== LÓGICA HORARIO (giro largo DER 2.8 s) ==");

  // ---------- 1.º color ----------
  Serial.println("[1] Esperando color...");
  char c1 = leerColorPaso(1, false, 0);

  if (c1=='G') {
    // VERDE → IZQ 1.4 → DER 1.4 → DER 2.8 → centro → retro 1.0 → leer 2.º
    avanzarConGiro(SERVO_LEFT,  GREEN1_LEFT_MS);
    avanzarConGiro(SERVO_RIGHT, GREEN1_RIGHT_MS);
    giroLargoHorario();
    servoCentroTrasDer();
    retro(GREEN1_FINAL_RETRO);
  } else {
    // ROJO → DER 1.6 → IZQ 1.6 → quieto
    avanzarConGiro(SERVO_RIGHT, RED1_RIGHT_MS);
    avanzarConGiro(SERVO_LEFT,  RED1_LEFT_MS);
    StopMotor();
  }
  limpiarBufferCamara();

  // ---------- 2.º color ----------
  Serial.println("[2] Leyendo 2.º (reglas según 1.º)...");
  char c2;
  if (c1=='G') {
    // sin NINGUNO aquí (bloqueante)
    c2 = leerColorPaso(2, false, 0);
    if (c2=='G') {
      // IZQ 1.6 → DER 1.6 → quieto (servo=35)
      avanzarConGiro(SERVO_LEFT,  1600);
      avanzarConGiro(SERVO_RIGHT, 1600);
      servoCentroTrasDer(); StopMotor();
    } else { // ROJO
      avanzarConGiro(SERVO_RIGHT, 1600);
      avanzarConGiro(SERVO_LEFT,  1600);
      servoCentroTrasIzq(); StopMotor();
    }
  } else {
    // 1.º=ROJO: admite NINGUNO con maniobra especial
    c2 = leerColorPaso(2, true, WAIT_NO_COLOR_MS);
    if (c2=='G') {
      // recto 1.0 → DER 2.8 → quieto
      avanzarRecto(SEG_1S, SERVO_CENTER);
      giroLargoHorario();
      servoCentroTrasDer(); StopMotor();
    } else if (c2=='R') {
      // retro 0.3 → DER 2.8 → quieto
      retro(RETRO_CORTO_MS);
      giroLargoHorario();
      servoCentroTrasDer(); StopMotor();
    } else { // N
      maniobraEspecialHorario();
      limpiarBufferCamara();
      // reintento MISMO índice
      c2 = leerColorPaso(2, true, WAIT_NO_COLOR_MS);
      // vuelve a aplicar la rama (para no duplicar, haremos una mini-llamada recursiva simple)
      if (c2=='G') { avanzarRecto(SEG_1S,SERVO_CENTER); giroLargoHorario(); servoCentroTrasDer(); StopMotor(); }
      else if (c2=='R'){ retro(RETRO_CORTO_MS); giroLargoHorario(); servoCentroTrasDer(); StopMotor(); }
      else { /* si vuelve N, ya quedó mejor posicionado; continúa */ }
    }
  }
  limpiarBufferCamara();

  // ---------- 3.º color ----------
  Serial.println("[3] Leyendo 3.º (depende de 2.º)...");
  char c3;
  bool permitirN3 = (c2=='G') ? true : true; // en horario, 3.º admite N en ambas ramas (según tu tabla)
  c3 = leerColorPaso(3, permitirN3, WAIT_NO_COLOR_MS);

  if (c2=='G') {
    if (c3=='R') {
      // DER 2.0 → IZQ 2.0 → quieto (servo=45)
      avanzarConGiro(SERVO_RIGHT, CONT_TURN_MS);
      avanzarConGiro(SERVO_LEFT,  CONT_TURN_MS);
      servoCentroTrasIzq(); StopMotor();
    } else { // VERDE o N
      // recto 2.0 → DER 2.8 → centro → retro 1.0
      avanzarRecto(CONT_FORWARD_MS, SERVO_CENTER);
      giroLargoHorario(); servoCentroTrasDer(); retro(1000);
    }
  } else { // c2=='R'
    if (c3=='G') {
      // IZQ 2.0 → DER 2.0 → recto 1.0 → DER 2.8 → centro → retro 1.0
      avanzarConGiro(SERVO_LEFT, CONT_TURN_MS);
      avanzarConGiro(SERVO_RIGHT,CONT_TURN_MS);
      avanzarRecto(SEG_1S, SERVO_CENTER);
      giroLargoHorario(); servoCentroTrasDer(); retro(1000);
    } else { // ROJO o N
      // recto 2.0 → quieto
      avanzarRecto(CONT_FORWARD_MS, SERVO_CENTER);
      StopMotor();
    }
  }
  limpiarBufferCamara();

  // ---------- 4.º color (ramificado por 2.º y 3.º) ----------
  Serial.println("[4] Leyendo 4.º...");
  // Reglas: (2=G,3=G|N), (2=G,3=R), (2=R,3=G), (2=R,3=R|N)
  bool permitirN4 = ((c2=='G' && c3!='R') || (c2=='R' && c3!='G')) ? false : false; // en tu última corrección removiste “Ninguno” en varias; lo dejamos sin N por defecto
  char c4 = leerColorPaso(4, permitirN4, WAIT_NO_COLOR_MS);

  if (c2=='G' && (c3=='G' || c3=='N')) {
    if (c4=='G') { avanzarConGiro(SERVO_LEFT,1600); avanzarConGiro(SERVO_RIGHT,1600); servoCentroTrasDer(); StopMotor(); }
    else         { avanzarConGiro(SERVO_RIGHT,1600); avanzarConGiro(SERVO_LEFT,1600);  servoCentroTrasIzq(); StopMotor(); }
  }
  else if (c2=='G' && c3=='R') {
    if (c4=='G') { avanzarRecto(SEG_1S,SERVO_CENTER); giroLargoHorario(); servoCentroTrasDer(); retro(1000); StopMotor(); }
    else         { giroLargoHorario(); servoCentroTrasDer(); retro(1000); StopMotor(); }
  }
  else if (c2=='R' && c3=='G') {
    if (c4=='G') { avanzarConGiro(SERVO_LEFT,1600); avanzarConGiro(SERVO_RIGHT,1600); servoCentroTrasDer(); StopMotor(); }
    else         { avanzarConGiro(SERVO_RIGHT,1600); avanzarConGiro(SERVO_LEFT,1600);  servoCentroTrasIzq(); StopMotor(); }
  }
  else { // (c2=='R' && (c3=='R' || c3=='N'))
    if (c4=='G') { avanzarRecto(SEG_1S,SERVO_CENTER); giroLargoHorario(); servoCentroTrasDer(); retro(1000); StopMotor(); }
    else         { giroLargoHorario(); servoCentroTrasDer(); retro(1000); StopMotor(); }
  }
  limpiarBufferCamara();

  // ---------- 5.º color ----------
  Serial.println("[5] Leyendo 5.º...");
  char c5 = leerColorPaso(5, true, WAIT_NO_COLOR_MS); // aquí sí admitimos N en la rama (4=G) per tabla

  // Si 4.º=G
  if (c4=='G') {
    if (c5=='R') {
      avanzarConGiro(SERVO_RIGHT, CONT_TURN_MS);
      avanzarConGiro(SERVO_LEFT,  CONT_TURN_MS);
      servoCentroTrasIzq(); StopMotor();
    } else { // G o N
      avanzarRecto(CONT_FORWARD_MS, SERVO_CENTER);
      giroLargoHorario(); servoCentroTrasDer(); retro(1000);
    }
  } else { // 4.º=R
    if (c5=='G') {
      avanzarConGiro(SERVO_LEFT, CONT_TURN_MS);
      avanzarConGiro(SERVO_RIGHT,CONT_TURN_MS);
      avanzarRecto(SEG_1S, SERVO_CENTER);
      giroLargoHorario(); servoCentroTrasDer(); retro(1000);
    } else { // R o N
      avanzarRecto(CONT_FORWARD_MS, SERVO_CENTER); StopMotor();
    }
  }
  limpiarBufferCamara();

  // ---------- 6.º color ----------
  Serial.println("[6] Leyendo 6.º...");
  char c6 = leerColorPaso(6, false, 0); // en 6.º (según tu última versión) no forzamos N salvo cuando 5º=R se añadió N especial, ya se usó en 5.º
  if (c5=='G') {
    if (c6=='G') { avanzarConGiro(SERVO_LEFT,1600); avanzarConGiro(SERVO_RIGHT,1600); servoCentroTrasDer(); StopMotor(); }
    else         { avanzarConGiro(SERVO_RIGHT,1600); avanzarConGiro(SERVO_LEFT,1600);  servoCentroTrasIzq(); StopMotor(); }
  } else { // 5.º=R o N
    if (c6=='G') { avanzarRecto(SEG_1S,SERVO_CENTER); giroLargoHorario(); servoCentroTrasDer(); retro(1000); StopMotor(); }
    else         { giroLargoHorario(); servoCentroTrasDer(); retro(1000); StopMotor(); }
  }
  limpiarBufferCamara();

  // ---------- 7.º color ----------
  Serial.println("[7] Leyendo 7.º...");
  char c7 = leerColorPaso(7, false, 0);
  if (c6=='G') {
    if (c7=='G') { avanzarRecto(CONT_FORWARD_MS, SERVO_CENTER); giroLargoHorario(); servoCentroTrasDer(); retro(1000); }
    else         { avanzarConGiro(SERVO_RIGHT,CONT_TURN_MS); avanzarConGiro(SERVO_LEFT,CONT_TURN_MS); servoCentroTrasIzq(); StopMotor(); }
  } else {
    if (c7=='G') {
      avanzarConGiro(SERVO_LEFT,CONT_TURN_MS);
      avanzarConGiro(SERVO_RIGHT,CONT_TURN_MS);
      avanzarRecto(SEG_1S, SERVO_CENTER);
      giroLargoHorario(); servoCentroTrasDer(); retro(1000);
    } else {
      avanzarRecto(CONT_FORWARD_MS, SERVO_CENTER); StopMotor();
    }
  }
  limpiarBufferCamara();

  // ---------- 8.º color (regla especial horario) ----------
  Serial.println("[8] Leyendo 8.º (regla especial)...");
  char c8 = leerColorPaso(8, false, 0); // no importa el color para el final, pero dejamos lectura por consistencia

  // Regla especial que pediste para HORARIO:
  // Si 7.º = ROJO → (aquí iría maniobra especial) y luego avanza 1 s
  // Si 7.º = VERDE → solo avanza 1 s
  if (c7=='R') {
    maniobraEspecialHorario();
    avanzarRecto(SEG_1S, SERVO_CENTER);
  } else {
    avanzarRecto(SEG_1S, SERVO_CENTER);
  }
  StopMotor();
}

// =================== Núcleo de lógica: ANTIHORARIO ===================
void ejecutarAntiHorario() {
  Serial.println("== LÓGICA ANTIHORARIO (giro largo IZQ 2.8 s) ==");

  // ---------- 1.º color ----------
  Serial.println("[1] Esperando color...");
  char c1 = leerColorPaso(1, false, 0);

  if (c1=='R') {
    // ROJO → DER 1.4 → IZQ 1.4 → IZQ 2.8 → centro(45) → retro 1.0
    avanzarConGiro(SERVO_RIGHT, 1400);
    avanzarConGiro(SERVO_LEFT,  1400);
    giroLargoAntiHorario();
    servoCentroTrasIzq();
    retro(1000);
  } else {
    // VERDE → IZQ 1.6 → DER 1.6 → quieto
    avanzarConGiro(SERVO_LEFT, 1600);
    avanzarConGiro(SERVO_RIGHT,1600);
    StopMotor();
  }
  limpiarBufferCamara();

  // ---------- 2.º color (pauta replicable en 4.º y 6.º) ----------
  Serial.println("[2] Leyendo 2.º (depende de 1.º)...");
  char c2;
  if (c1=='G') {
    // admite N con maniobra especial ANTIHO
    c2 = leerColorPaso(2, true, WAIT_NO_COLOR_MS);
    if (c2=='G') {
      retro(RETRO_CORTO_MS);
      giroLargoAntiHorario(); servoCentroTrasIzq(); retro(1000);
    } else if (c2=='R') {
      avanzarRecto(SEG_1S, SERVO_CENTER);
      giroLargoAntiHorario(); servoCentroTrasIzq(); retro(1000);
    } else {
      maniobraEspecialAntiHo();
      limpiarBufferCamara();
      // reintento MISMO índice
      c2 = leerColorPaso(2, true, WAIT_NO_COLOR_MS);
      if (c2=='G'){ retro(RETRO_CORTO_MS); giroLargoAntiHorario(); servoCentroTrasIzq(); retro(1000); }
      else if (c2=='R'){ avanzarRecto(SEG_1S,SERVO_CENTER); giroLargoAntiHorario(); servoCentroTrasIzq(); retro(1000); }
    }
  } else {
    // 1.º=ROJO: sin “ninguno”
    c2 = leerColorPaso(2, false, 0);
    if (c2=='G') {
      avanzarConGiro(SERVO_LEFT,1600);
      avanzarConGiro(SERVO_RIGHT,1600);
      StopMotor();
    } else {
      avanzarConGiro(SERVO_RIGHT,1600);
      avanzarConGiro(SERVO_LEFT,1600);
      StopMotor();
    }
  }
  limpiarBufferCamara();

  // ---------- 3.º color (pauta replicable en 5.º y 7.º) ----------
  Serial.println("[3] Leyendo 3.º (depende de 2.º)...");
  char c3 = leerColorPaso(3, true, WAIT_NO_COLOR_MS); // aquí sí usamos N

  if (c2=='R' || c2=='N') {
    if (c3=='G') {
      avanzarConGiro(SERVO_LEFT,CONT_TURN_MS);
      avanzarConGiro(SERVO_RIGHT,CONT_TURN_MS);
      StopMotor();
    } else {
      avanzarRecto(CONT_FORWARD_MS, SERVO_CENTER);
      giroLargoAntiHorario(); servoCentroTrasIzq(); retro(1000);
    }
  } else { // c2==G
    if (c3=='R') {
      avanzarConGiro(SERVO_RIGHT,CONT_TURN_MS);
      avanzarConGiro(SERVO_LEFT, CONT_TURN_MS);
      giroLargoAntiHorario(); servoCentroTrasIzq(); retro(1000);
    } else { // G o N
      avanzarRecto(CONT_FORWARD_MS, SERVO_CENTER);
      StopMotor();
    }
  }
  limpiarBufferCamara();

  // ---------- 4.º color ----------
  Serial.println("[4] Leyendo 4.º...");
  char c4;
  if (c3=='R') {
    c4 = leerColorPaso(4, false, 0);
    if (c4=='G') { avanzarConGiro(SERVO_LEFT,1600); avanzarConGiro(SERVO_RIGHT,1600); StopMotor(); }
    else         { avanzarConGiro(SERVO_RIGHT,1600); avanzarConGiro(SERVO_LEFT,1600);  StopMotor(); }
  } else { // 3.º = VERDE o N → con “ninguno” = maniobra especial ANTIHO
    c4 = leerColorPaso(4, true, WAIT_NO_COLOR_MS);
    if (c4=='R') { avanzarRecto(SEG_1S,SERVO_CENTER); giroLargoAntiHorario(); servoCentroTrasIzq(); retro(1000); StopMotor(); }
    else if (c4=='G'){ giroLargoAntiHorario(); servoCentroTrasIzq(); retro(1000); StopMotor(); }
    else {
      maniobraEspecialAntiHo();
      limpiarBufferCamara();
      // reintenta 4.º
      c4 = leerColorPaso(4, true, WAIT_NO_COLOR_MS);
      if (c4=='R') { avanzarRecto(SEG_1S,SERVO_CENTER); giroLargoAntiHorario(); servoCentroTrasIzq(); retro(1000); StopMotor(); }
      else if (c4=='G'){ giroLargoAntiHorario(); servoCentroTrasIzq(); retro(1000); StopMotor(); }
    }
  }
  limpiarBufferCamara();

  // ---------- 5.º color ----------
  Serial.println("[5] Leyendo 5.º...");
  char c5 = leerColorPaso(5, true, WAIT_NO_COLOR_MS);
  if (c4=='G') {
    if (c5=='R') {
      avanzarConGiro(SERVO_RIGHT,CONT_TURN_MS);
      avanzarConGiro(SERVO_LEFT, CONT_TURN_MS);
      StopMotor();
    } else { // G o N
      avanzarRecto(CONT_FORWARD_MS, SERVO_CENTER);
      giroLargoAntiHorario(); servoCentroTrasIzq(); retro(1000);
    }
  } else { // 4.º = R
    if (c5=='G') {
      avanzarConGiro(SERVO_LEFT,CONT_TURN_MS);
      avanzarConGiro(SERVO_RIGHT,CONT_TURN_MS);
      // luego IZQ 2.8
      giroLargoAntiHorario(); servoCentroTrasIzq(); retro(1000);
    } else { // R o N
      avanzarRecto(CONT_FORWARD_MS, SERVO_CENTER); StopMotor();
    }
  }
  limpiarBufferCamara();

  // ---------- 6.º color ----------
  Serial.println("[6] Leyendo 6.º...");
  char c6 = leerColorPaso(6, true, WAIT_NO_COLOR_MS);
  if (c5=='G') {
    if (c6=='G') { avanzarConGiro(SERVO_LEFT,1600); avanzarConGiro(SERVO_RIGHT,1600); StopMotor(); }
    else if (c6=='R'){ avanzarConGiro(SERVO_RIGHT,1600); avanzarConGiro(SERVO_LEFT,1600);  StopMotor(); }
    else { // N
      avanzarRecto(CONT_FORWARD_MS, SERVO_CENTER);
      giroLargoAntiHorario(); servoCentroTrasIzq(); retro(1000);
    }
  } else { // 5.º=R o N
    if (c6=='G') { avanzarRecto(SEG_1S,SERVO_CENTER); giroLargoAntiHorario(); servoCentroTrasIzq(); retro(1000); StopMotor(); }
    else if (c6=='R'){ giroLargoAntiHorario(); servoCentroTrasIzq(); retro(1000); StopMotor(); }
    else { // N
      avanzarRecto(CONT_FORWARD_MS, SERVO_CENTER);
      giroLargoAntiHorario(); servoCentroTrasIzq(); retro(1000);
    }
  }
  limpiarBufferCamara();

  // ---------- 7.º color ----------
  Serial.println("[7] Leyendo 7.º...");
  char c7 = leerColorPaso(7, true, WAIT_NO_COLOR_MS);
  if (c6=='G') {
    if (c7=='G') { avanzarRecto(CONT_FORWARD_MS,SERVO_CENTER); giroLargoAntiHorario(); servoCentroTrasIzq(); retro(1000); }
    else if (c7=='R'){ avanzarConGiro(SERVO_RIGHT,CONT_TURN_MS); avanzarConGiro(SERVO_LEFT,CONT_TURN_MS); StopMotor(); }
    else { // N
      avanzarRecto(CONT_FORWARD_MS,SERVO_CENTER); giroLargoAntiHorario(); servoCentroTrasIzq(); retro(1000);
    }
  } else { // 6.º=R o N
    if (c7=='G') {
      avanzarConGiro(SERVO_LEFT,CONT_TURN_MS);
      avanzarConGiro(SERVO_RIGHT,CONT_TURN_MS);
      giroLargoAntiHorario(); servoCentroTrasIzq(); retro(1000);
    } else if (c7=='R') {
      avanzarRecto(CONT_FORWARD_MS,SERVO_CENTER); StopMotor();
    } else {
      avanzarRecto(CONT_FORWARD_MS,SERVO_CENTER); StopMotor();
    }
  }
  limpiarBufferCamara();

  // ---------- 8.º color (regla especial antiho) ----------
  Serial.println("[8] Leyendo 8.º (regla especial)...");
  char c8 = leerColorPaso(8, false, 0);

  // Regla especial ANTIHO:
  // Si 7.º = VERDE → maniobra especial antiho y luego avanza 1 s
  // Si 7.º = ROJO  → solo avanza 1 s
  if (c7=='G') {
    maniobraEspecialAntiHo();
    avanzarRecto(SEG_1S, SERVO_CENTER);
  } else {
    avanzarRecto(SEG_1S, SERVO_CENTER);
  }
  StopMotor();
}

// =================== Secuencia de una vuelta (1..8) ===================
void ejecutarVuelta(Sentido s) {
  if (s==HORARIO) ejecutarHorario();
  else            ejecutarAntiHorario();
}

// =================== Setup ===================
void setup() {
  Serial.begin(115200);
  Wire.begin();

  // UART cámara
  Serial1.begin(CAM_BAUD, SERIAL_8N1, CAM_RX, CAM_TX);

  // Pines motor
  pinMode(SHCP_PIN, OUTPUT);
  pinMode(EN_PIN,   OUTPUT);
  pinMode(DATA_PIN, OUTPUT);
  pinMode(STCP_PIN, OUTPUT);
  pinMode(PWM1_PIN, OUTPUT);

  // Servo
  miServo.setPeriodHertz(50);
  miServo.attach(SERVO_PIN, 500, 2400);
  miServo.write(SERVO_CENTER);
  StopMotor();

  // VL53
  selectOnlyOneMux(MUX_LEFT_ADDR);
  sensorLeft.setTimeout(250); sensorLeft.init();
  sensorLeft.setDistanceMode(VL53L1X::Long);
  sensorLeft.setMeasurementTimingBudget(50000);
  sensorLeft.startContinuous(50);

  selectOnlyOneMux(MUX_RIGHT_ADDR);
  sensorRight.setTimeout(250); sensorRight.init();
  sensorRight.setDistanceMode(VL53L1X::Long);
  sensorRight.setMeasurementTimingBudget(50000);
  sensorRight.startContinuous(50);

  Serial.println("== Inicio: Salida estacionamiento ==");
  // Elegir lado por mayor distancia
  int dL = lecturaPromedio(sensorLeft,  MUX_LEFT_ADDR, 3);
  int dR = lecturaPromedio(sensorRight, MUX_RIGHT_ADDR,3);
  Serial.print("Dist IZQ="); Serial.print(dL);
  Serial.print(" | DER=");   Serial.println(dR);

  bool eligioIzquierda = (dL >= dR);
  if (eligioIzquierda) {
    Serial.println("Salida: IZQUIERDA (=> ANTIHORARIO)");
    secuenciaSalidaIzquierda();
    sentido = ANTIHORARIO;
  } else {
    Serial.println("Salida: DERECHA (=> HORARIO)");
    secuenciaSalidaDerecha();
    sentido = HORARIO;
  }

  Serial.println("Maniobra final (giro contrario)...");
  maniobraFinal(eligioIzquierda);

  Serial.println("== Preparado para Vuelta 1 ==");
}

// =================== Loop ===================
void loop() {
  // Vuelta 1 (lee cámara y memoriza)
  if (vueltaActual == 1) {
    usarMemoria = false;
    ejecutarVuelta(sentido);
    memoriaLlena = true;
    vueltaActual = 2;
    Serial.println("== Fin Vuelta 1. Memoria lista. Comienza Vuelta 2 ==");
    delay(400);
    return;
  }

  // Vuelta 2 (reproduce memoria)
  if (vueltaActual == 2 && memoriaLlena) {
    usarMemoria = true;
    ejecutarVuelta(sentido);
    vueltaActual = 3;
    Serial.println("== Fin Vuelta 2. Comienza Vuelta 3 ==");
    delay(400);
    return;
  }

  // Vuelta 3 (reproduce memoria)
  if (vueltaActual == 3 && memoriaLlena) {
    usarMemoria = true;
    ejecutarVuelta(sentido);
    Serial.println("== Fin Vuelta 3. Programa finaliza ==");
    while (true) { StopMotor(); delay(1000); }
  }

  // Seguridad
  StopMotor();
  delay(1000);
}

```

Camera
----

The camera is programmed to detect the red and green colors, the camera has other functions but for the sake of simplicity we only used in to detect colors. The camera was programmed with Arduino

```arduino

from machine import UART
import sensor
import image
import time

UART a ESP32 (TX en P4)
uart = UART(1, baudrate=115200)

Configuración de la cámara
sensor.reset()
sensor.set_pixformat(sensor.RGB565)
sensor.set_framesize(sensor.HD720)
sensor.skip_frames(time=2000)
sensor.set_auto_gain(False)
sensor.set_auto_whitebal(False)

Umbrales
red_threshold = (30, 100, 15, 127, 15, 127)
green_threshold = (30, 100, -127, -15, 15, 127)

clock = time.clock()

while True:
    clock.tick()
    img = sensor.snapshot()

    # Detectar rojo (máximo 1)
    rojos = img.find_blobs([red_threshold], pixels_threshold=200, area_threshold=200, merge=True)
    verdes = img.find_blobs([green_threshold], pixels_threshold=200, area_threshold=200, merge=True)

    if len(rojos) > 0:
        blob = rojos[0]
        img.draw_rectangle(blob.rect(), color=(255, 0, 0))
        img.draw_cross(blob.cx(), blob.cy(), color=(255, 0, 0))
        uart.write("ROJO\n")
        print("ROJO")
    elif len(verdes) > 0:
        blob = verdes[0]
        img.draw_rectangle(blob.rect(), color=(0, 255, 0))
        img.draw_cross(blob.cx(), blob.cy(), color=(0, 255, 0))
        uart.write("VERDE\n")
        print("VERDE")

    time.sleep_ms(300)  # Da tiempo al ESP32 a leer sin saturarse

```

(Update) This part of the code trades fps for quality to make it easier to detect the color blocks, it uses the inferior part of the camera so it can see the ground and it ignores the the servo motor because the range of the camera can see the motor and the motor is colored so it could interfer with the reading.

```python

from machine import UART
import sensor, image, time

# Configuración de UART para enviar los datos al ESP32
uart = UART(1, baudrate=115200)

# Inicialización del sensor de la cámara
sensor.reset()
sensor.set_pixformat(sensor.RGB565)  # Formato de color RGB
sensor.set_framesize(sensor.QVGA)  # Resolución más baja para mejorar FPS (160x120)
sensor.skip_frames(time=2000)  # Esperar 2 segundos para estabilizar la cámara
sensor.set_auto_gain(False)  # Desactivar ganancia automática para controlar la exposición
sensor.set_auto_whitebal(False)  # Desactivar balance de blancos automático

# Umbrales ajustados para evitar la confusión con naranja
red_threshold = (40, 100, 15, 127, 15, 127)  # Umbral rojo más restringido
green_threshold = (30, 100, -127, -15, 15, 127)  # Umbral verde

# Variables para controlar el envío de datos
ultimo_color = ""
tiempo_ultimo_envio = time.ticks_ms()
intervalo = 10000  # Intervalo de 10 segundos entre envíos de color

# Función para ajustar la exposición y mejorar la detección bajo diferentes condiciones de luz
def ajustar_iluminacion():
    img = sensor.snapshot()
    promedio = 0
    for pixel in img:
        promedio += pixel[0]  # Tomar un valor de la componente R (Rojo)
    promedio = promedio // (img.width() * img.height())  # Promedio de la imagen

    # Ajustar la ganancia en función de la iluminación
    if promedio < 100:  # Condición de poca luz
        sensor.set_auto_gain(True)
    else:
        sensor.set_auto_gain(False)

# Función para detectar los colores usando find_blobs (más eficiente)
def detectar_color_blobs(img):
    # Limitar la región a la parte superior de la imagen (evitar la franja en el piso)
    region_superior = (0, 0, img.width(), img.height() // 2)  # Tomar solo la mitad superior de la imagen

    rojos = img.find_blobs([red_threshold], pixels_threshold=100, area_threshold=100, merge=True, roi=region_superior)
    verdes = img.find_blobs([green_threshold], pixels_threshold=100, area_threshold=100, merge=True, roi=region_superior)
    return rojos, verdes

while True:
    # Ajustar la iluminación según el entorno
    ajustar_iluminacion()

    # Capturar una nueva imagen
    img = sensor.snapshot()

    # Detectar rojo y verde usando blobs (más eficiente)
    rojos, verdes = detectar_color_blobs(img)

    # Filtrar los blobs para encontrar los que tengan un tamaño adecuado (aproximadamente 10 cm de alto)
    rojos_validos = [blob for blob in rojos if blob[3] >= 10]  # Filtrar bloques que sean al menos 10 píxeles de alto
    verdes_validos = [blob for blob in verdes if blob[3] >= 10]  # Filtrar bloques que sean al menos 10 píxeles de alto

    # Determinar el color detectado
    color_detectado = ""
    if len(rojos_validos) > len(verdes_validos):
        color_detectado = "ROJO"
    elif len(verdes_validos) > len(rojos_validos):
        color_detectado = "VERDE"

    # Enviar el color detectado si ha cambiado o si ha pasado el intervalo de tiempo
    if color_detectado:
        tiempo_actual = time.ticks_ms()
        if (color_detectado != ultimo_color) or (time.ticks_diff(tiempo_actual, tiempo_ultimo_envio) > intervalo):
            uart.write(color_detectado + "\n")  # Enviar el color por UART
            print("Color enviado:", color_detectado)
            ultimo_color = color_detectado
            tiempo_ultimo_envio = tiempo_actual
    else:
        ultimo_color = ""  # Reiniciar si no se detecta ningún color

```

(Update) Now it only sees half of its visor and it only detects the color closest to it

```python

from machine import UART
import sensor, image, time

# Configuración de UART para enviar los datos al ESP32
uart = UART(1, baudrate=115200)

# Inicialización del sensor de la cámara
sensor.reset()
sensor.set_pixformat(sensor.RGB565)  # Formato de color RGB
sensor.set_framesize(sensor.QVGA)  # Resolución más baja para mejorar FPS (320x240)
sensor.skip_frames(time=2000)  # Esperar 2 segundos para estabilizar la cámara
sensor.set_auto_gain(False)  # Desactivar ganancia automática para controlar la exposición
sensor.set_auto_whitebal(False)  # Desactivar balance de blancos automático

# Umbrales ajustados para evitar la confusión con naranja
red_threshold = (30, 100, 15, 127, 15, 127)  # Umbral rojo más restringido
green_threshold = (30, 100, -127, -15, 15, 127)  # Umbral verde

# Variables para controlar el envío de datos
ultimo_color = ""
tiempo_ultimo_envio = time.ticks_ms()
intervalo = 10000  # Intervalo de 10 segundos entre envíos de color

# Función para ajustar la exposición y mejorar la detección bajo diferentes condiciones de luz
def ajustar_iluminacion():
    img = sensor.snapshot()
    promedio = 0
    for pixel in img:
        promedio += pixel[0]  # Tomar un valor de la componente R (Rojo)
    promedio = promedio // (img.width() * img.height())  # Promedio de la imagen

    # Ajustar la ganancia en función de la iluminación
    if promedio < 100:  # Condición de poca luz
        sensor.set_auto_gain(True)
    else:
        sensor.set_auto_gain(False)

# Función para detectar los colores usando find_blobs (más eficiente)
def detectar_color_blobs(img):
    # Limitar la región a los 3/4 superiores de la imagen (evitar la franja en el piso)
    region_superior = (0, 0, img.width(), img.height() // 2)  # Usar solo la mitad superior de la imagen

    rojos = img.find_blobs([red_threshold], pixels_threshold=100, area_threshold=100, merge=True, roi=region_superior)
    verdes = img.find_blobs([green_threshold], pixels_threshold=100, area_threshold=100, merge=True, roi=region_superior)
    return rojos, verdes

# Función para obtener el blob más cercano
def obtener_blob_mas_cercano(rojos, verdes):
    # Verificar que haya blobs en ambos colores
    if not rojos and not verdes:
        return None, None

    # Encontrar el blob más cercano (el que tiene el valor de 'y' más bajo)
    rojo_cercano = min(rojos, key=lambda b: b[1], default=None)  # Minimo valor de 'y' para los rojos
    verde_cercano = min(verdes, key=lambda b: b[1], default=None)  # Minimo valor de 'y' para los verdes

    # Comparar cuál de los dos colores está más cerca
    if rojo_cercano and verde_cercano:
        if rojo_cercano[1] < verde_cercano[1]:  # Si el rojo está más cerca
            return "ROJO", rojo_cercano
        else:  # Si el verde está más cerca
            return "VERDE", verde_cercano
    elif rojo_cercano:  # Si solo se detecta rojo
        return "ROJO", rojo_cercano
    elif verde_cercano:  # Si solo se detecta verde
        return "VERDE", verde_cercano
    return None, None

while True:
    # Ajustar la iluminación según el entorno
    ajustar_iluminacion()

    # Capturar una nueva imagen
    img = sensor.snapshot()

    # Detectar rojo y verde usando blobs (más eficiente)
    rojos, verdes = detectar_color_blobs(img)

    # Filtrar los blobs para encontrar los que tengan un tamaño adecuado (aproximadamente 10 cm de alto)
    rojos_validos = [blob for blob in rojos if blob[3] >= 10]  # Filtrar bloques que sean al menos 10 píxeles de alto
    verdes_validos = [blob for blob in verdes if blob[3] >= 10]  # Filtrar bloques que sean al menos 10 píxeles de alto

    # Obtener el blob más cercano
    color_detectado, blob_detectado = obtener_blob_mas_cercano(rojos_validos, verdes_validos)

    # Si se ha detectado un color, dibujar el marco y enviar el color
    if color_detectado and blob_detectado:
        # Dibujar un rectángulo alrededor del blob más cercano
        img.draw_rectangle(blob_detectado[0], blob_detectado[1], blob_detectado[2], blob_detectado[3], color=(255, 0, 0))  # Rojo
        img.draw_string(blob_detectado[0], blob_detectado[1] - 10, color_detectado, color=(255, 0, 0))  # Etiqueta con el color

        # Enviar el color detectado si ha cambiado o si ha pasado el intervalo de tiempo
        tiempo_actual = time.ticks_ms()
        if (color_detectado != ultimo_color) or (time.ticks_diff(tiempo_actual, tiempo_ultimo_envio) > intervalo):
            uart.write(color_detectado + "\n")  # Enviar el color por UART
            print("Color enviado:", color_detectado)
            ultimo_color = color_detectado
            tiempo_ultimo_envio = tiempo_actual
    else:
        ultimo_color = ""  # Reiniciar si no se detecta ningún color

```

Camera code (FINAL)

This is the last update to the code before the 2025 national competition in Panama, the camera is now programmed for quality and precision rather than fps.

```python

# OpenMV color detector for ESP32 robot
# Sends: b"verde\n" or b"rojo\n" via UART(1) @ 115200
# Shows live overlay (rectangles + labels) in the OpenMV IDE preview.

from machine import UART
import sensor, image, time
from collections import deque

# ------------- UART to ESP32 -------------
# On most OpenMV boards, UART(1) uses P4/P5 (check your board silkscreen).
uart = UART(1, baudrate=115200, timeout_char=100)

# ------------- Camera setup -------------
sensor.reset()
sensor.set_pixformat(sensor.RGB565)          # color
sensor.set_framesize(sensor.QVGA)            # 320x240 for speed
sensor.set_auto_gain(False)                  # IMPORTANT: keep OFF for color thresholds
sensor.set_auto_whitebal(False)              # IMPORTANT: keep OFF for color thresholds
sensor.skip_frames(time=500)                 # small warmup so it starts almost immediately
clock = time.clock()

# ------------- Tuned LAB thresholds -------------
# These ranges are robust against a white track (white has a~0, b~0; we push away from that).
# Tweak here if your lighting is very different:
# Tuple format: (Lmin, Lmax, Amin, Amax, Bmin, Bmax)
RED_T   = (15, 85,   25, 127,  -10, 127)
GREEN_T = (10, 85, -128, -20,   -10, 127)

# ------------- Detection ROI -------------
# We ignore borders and most of the floor to avoid noise.
# ROI covers center 60% width and top 75% height (reduce masked area as you requested).
def compute_roi(img):
    w, h = img.width(), img.height()
    roi_x = int(w * 0.20)
    roi_y = 0
    roi_w = int(w * 0.60)
    roi_h = int(h * 0.75)
    return (roi_x, roi_y, roi_w, roi_h)

# ------------- Sensitivity & stability -------------
PIXELS_THRESHOLD = 60     # lower -> more sensitive (min connected pixels)
AREA_THRESHOLD   = 80     # lower -> more sensitive (min bounding box area)
MIN_H_PX         = 10     # ignore tiny blobs by height
REFRESH_MS       = 400    # resend color at least every 0.4s even if unchanged
DEBOUNCE_N       = 5      # frames for majority vote
DEBOUNCE_K       = 3      # need >= K of last N frames to accept a new label

last_sent_label  = None
last_send_time   = time.ticks_ms()
history          = deque(maxlen=DEBOUNCE_N)

# ------------- Optional: mild adaptive exposure (keeps colors readable) -------------
# We make tiny adjustments without enabling full auto-gain/auto-WB (which would break color thresholds).
def mild_exposure_nudge(img):
    # Compute statistics in the ROI to judge brightness
    roi = compute_roi(img)
    stats = img.get_statistics(roi=roi)
    # Luma proxy via mean of RGB565 is coarse; we use l_mean from LAB using .statistics() in RGB is not direct.
    # Simple heuristic: if very dark, briefly allow auto gain to catch up, then turn it off.
    global auto_gain_counter
    l_estimate = (stats.mean())  # 0..255 rough
    if l_estimate < 55:
        sensor.set_auto_gain(True)
    else:
        sensor.set_auto_gain(False)

# ------------- Pick the "closest" blob -------------
# We use the smallest y (higher on the image) as "closer" in your usage
def pick_blob(blobs):
    if not blobs:
        return None
    return min(blobs, key=lambda b: b.y())

def label_from_frame(img):
    roi = compute_roi(img)

    rojos = img.find_blobs([RED_T], pixels_threshold=PIXELS_THRESHOLD,
                           area_threshold=AREA_THRESHOLD, merge=True, roi=roi)
    verdes = img.find_blobs([GREEN_T], pixels_threshold=PIXELS_THRESHOLD,
                            area_threshold=AREA_THRESHOLD, merge=True, roi=roi)

    # Filter tiny blobs by height
    rojos  = [b for b in rojos  if b.h() >= MIN_H_PX]
    verdes = [b for b in verdes if b.h() >= MIN_H_PX]

    br = pick_blob(rojos)
    bg = pick_blob(verdes)

    # Decide based on presence and vertical position
    if br is None and bg is None:
        return None, None
    if br is not None and bg is None:
        return "rojo", br
    if br is None and bg is not None:
        return "verde", bg

    # Both present: choose the one with smaller y() (higher in the image)
    if br.y() < bg.y():
        return "rojo", br
    else:
        return "verde", bg

def stable_vote_push(label):
    history.append(label)
    if history.count(label) >= DEBOUNCE_K:
        return True
    return False

def maybe_send(label):
    global last_sent_label, last_send_time
    now = time.ticks_ms()
    # Send if changed OR it's time to refresh
    if (label != last_sent_label) or (time.ticks_diff(now, last_send_time) >= REFRESH_MS):
        token = (label + "\n").encode()
        uart.write(token)
        print("TX:", label)  # also print to IDE serial
        last_sent_label = label
        last_send_time = now

# ------------- Main loop -------------
while True:
    clock.tick()
    img = sensor.snapshot()

    # Mild exposure nudge to keep detection robust without ruining thresholds
    mild_exposure_nudge(img)

    # Detect
    label, blob = label_from_frame(img)

    # Draw ROI
    rx, ry, rw, rh = compute_roi(img)
    img.draw_rectangle(rx, ry, rw, rh, color=(200, 200, 200))  # light ROI box

    if label is None:
        # Draw hint text
        img.draw_string(4, 4, "No color", color=(255, 255, 255), scale=1)
        # Reset vote history on no color (optional): allows quicker switching
        history.append(None)
    else:
        # Draw blob box + label
        color_draw = (0, 255, 0) if label == "verde" else (255, 0, 0)
        img.draw_rectangle(blob.rect(), color=color_draw, thickness=2)
        img.draw_cross(blob.cx(), blob.cy(), color=color_draw, size=5)
        img.draw_string(blob.x(), max(0, blob.y()-12), label, color=color_draw, scale=2)

        # Stability (debounce) + send
        if stable_vote_push(label):
            maybe_send(label)

    # Optional FPS overlay
    img.draw_string(4, img.height()-12, "FPS: %0.1f" % clock.fps(), color=(255,255,255), scale=1)

```

[Back to table of contents](#table-of-contents)

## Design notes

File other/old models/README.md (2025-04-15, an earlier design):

Models
====

This directory contains pictures of prototypes, pieces and electronics of the robot

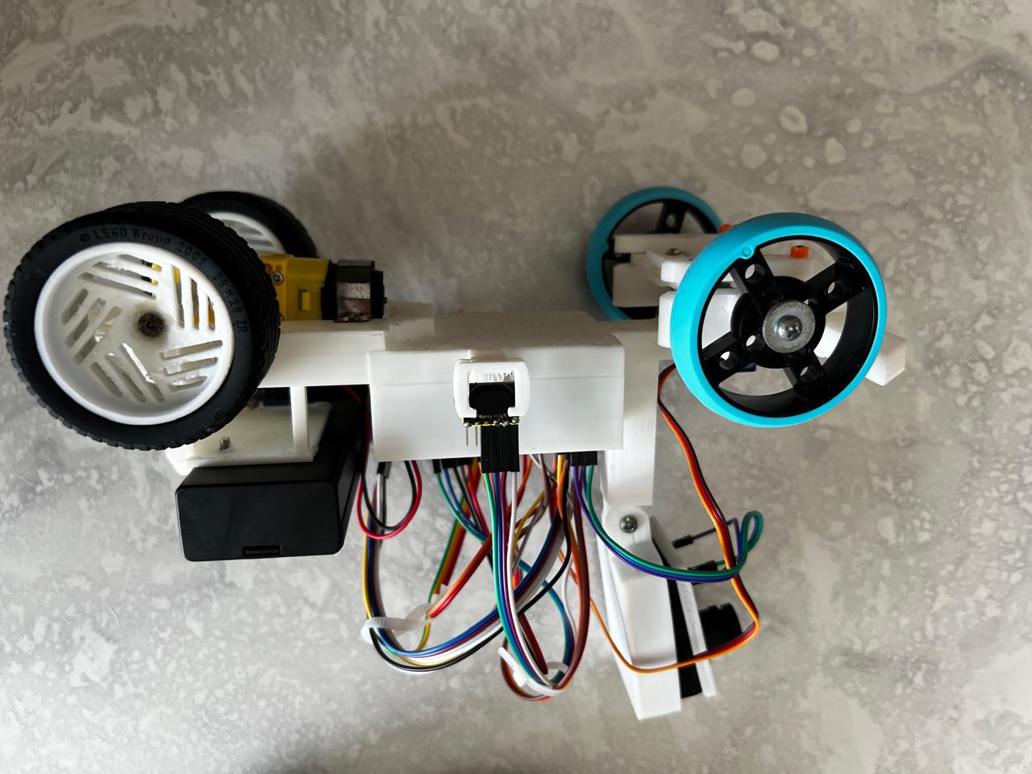
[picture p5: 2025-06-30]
v-photos/wro robot left.jpg

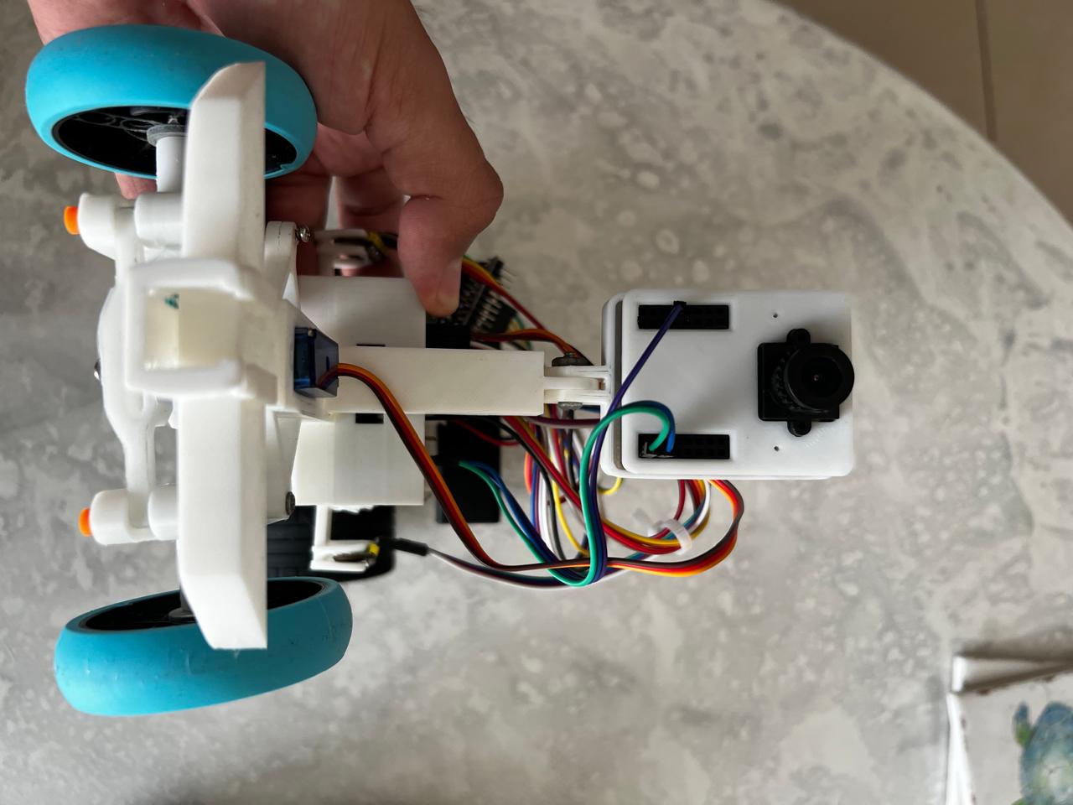
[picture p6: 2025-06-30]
v-photos/wro robot front.jpg

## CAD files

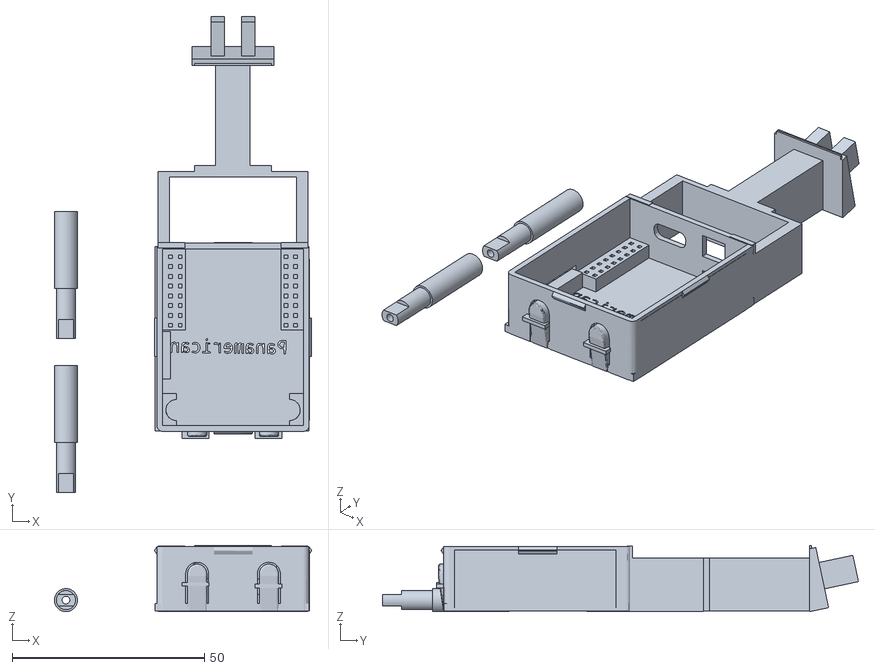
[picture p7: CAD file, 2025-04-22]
models/Body/Tremendous Fyyran-Kup.stl
66.8 x 123.7 x 17.2

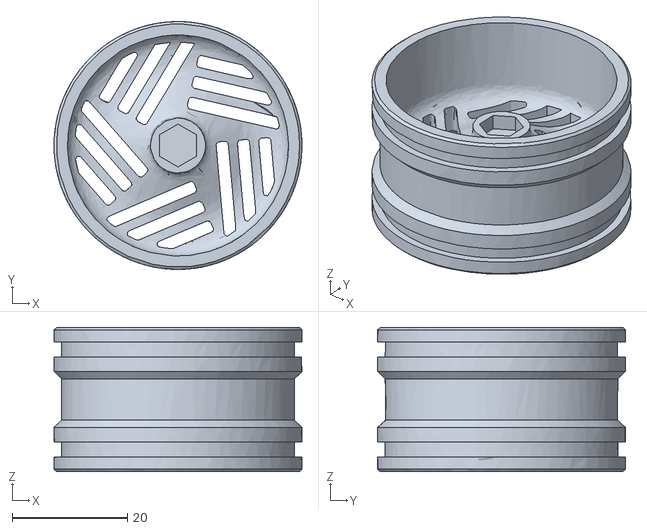
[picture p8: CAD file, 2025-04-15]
models/rims/Amazing Amberis-Uusam.stl
43.0 x 43.0 x 25.0

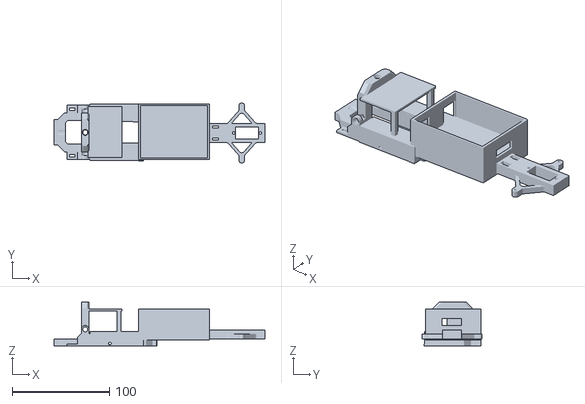
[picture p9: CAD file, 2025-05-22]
models/skeleton/Magnificent Stantia (2).stl
217.0 x 62.0 x 45.0

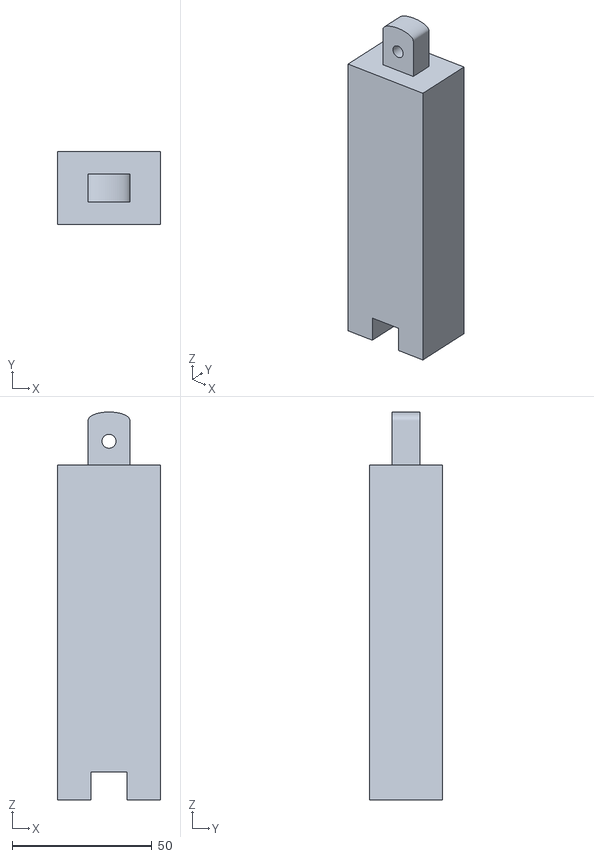
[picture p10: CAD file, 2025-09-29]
models/systems/Smooth Blorr.stl
37.0 x 26.0 x 139.0

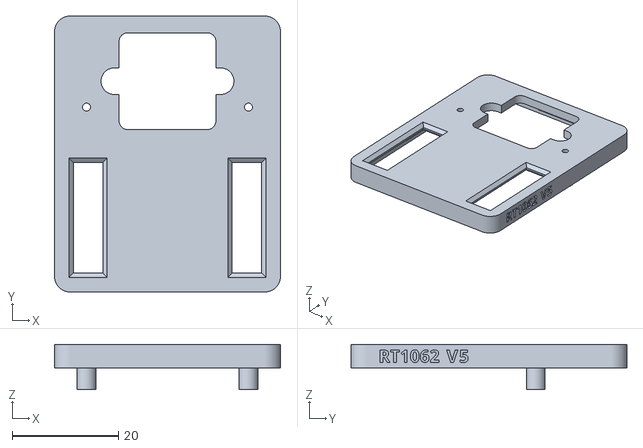
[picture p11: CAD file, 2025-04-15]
models/Body/RT1062 V5 Lid Open GPIO.stl
42.6 x 52.0 x 8.50

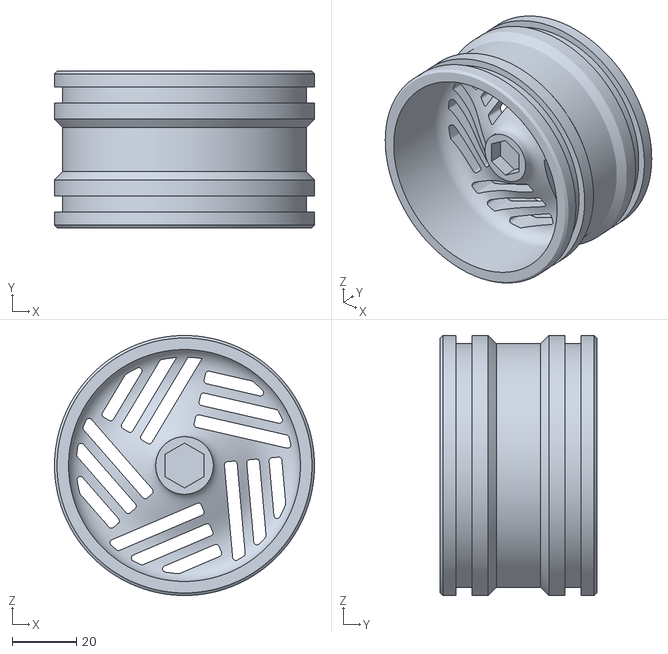
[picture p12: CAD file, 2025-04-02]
models/rims/rin de las llantas.stl
81.2 x 48.9 x 81.2

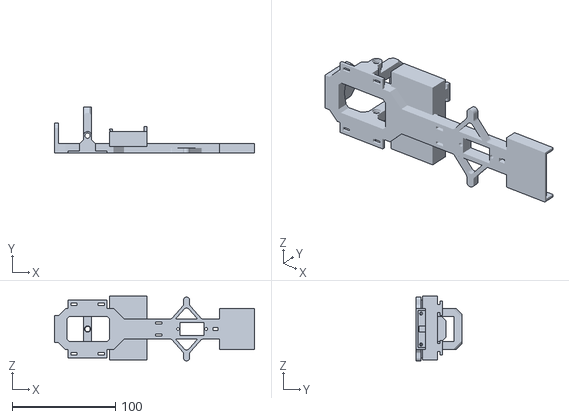
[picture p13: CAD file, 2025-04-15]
models/skeleton/chassis_v7 (1).stl
194.0 x 45.0 x 63.0

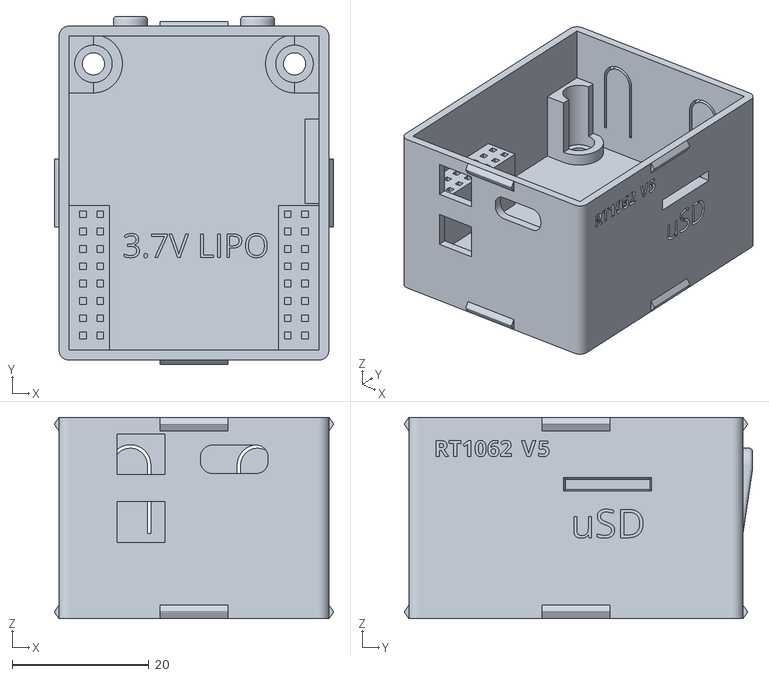
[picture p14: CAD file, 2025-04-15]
models/Body/RT1062 V5 Base.stl
40.9 x 51.0 x 29.5

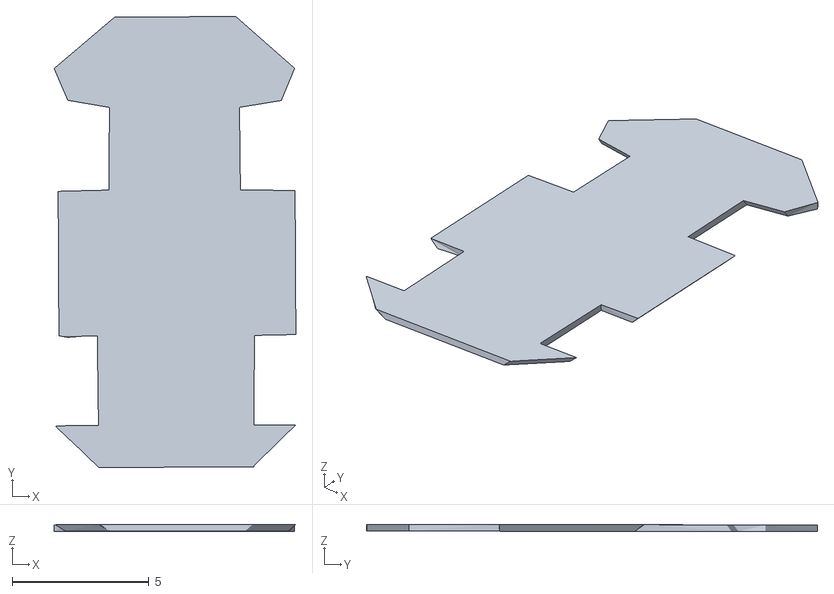
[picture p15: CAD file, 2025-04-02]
models/skeleton/modelaje 3D.stl
8.83 x 16.5 x 0.267

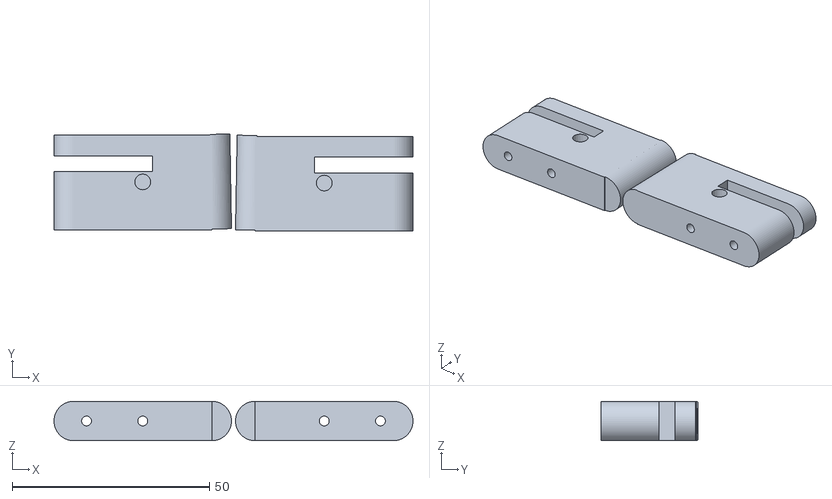
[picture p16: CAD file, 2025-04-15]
models/systems/Neat Wolt.stl
91.0 x 24.6 x 10.0

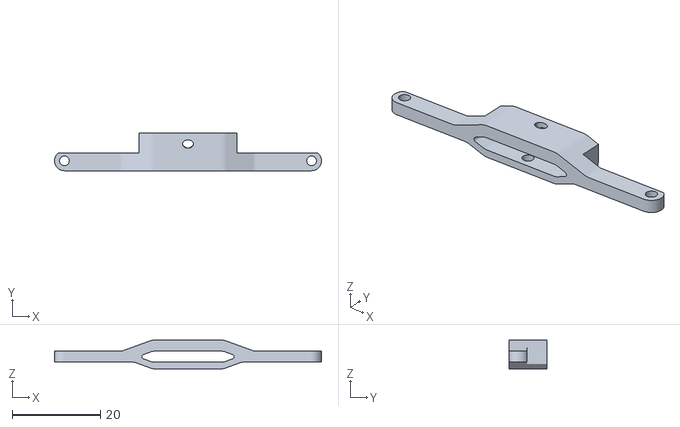
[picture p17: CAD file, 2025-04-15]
models/systems/Shiny Hillar.stl
60.5 x 8.50 x 6.50

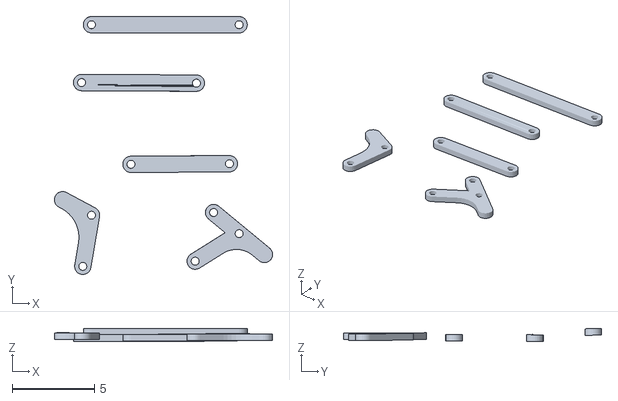
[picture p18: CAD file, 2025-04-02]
models/systems/Sistema de direccion.stl
13.3 x 15.7 x 0.781

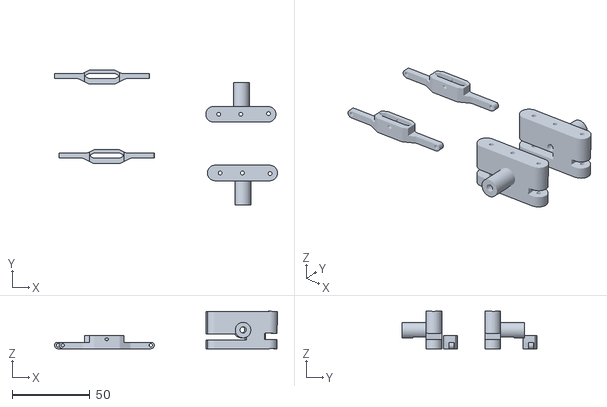
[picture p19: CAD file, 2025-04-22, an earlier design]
models/systems/Neat Wolt (3).stl
143.0 x 86.5 x 24.1

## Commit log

2025-04-15 Add files via upload
    First prototype of the robot
2025-06-30 Create camera
2025-07-31 Create camera (UPDATE)
2025-07-31 Create camera (UPDATE 2)
2025-07-31 Create camera (UPDATE 3)
2025-08-06 Update camera
2025-09-29 Create CAMERA FINAL
